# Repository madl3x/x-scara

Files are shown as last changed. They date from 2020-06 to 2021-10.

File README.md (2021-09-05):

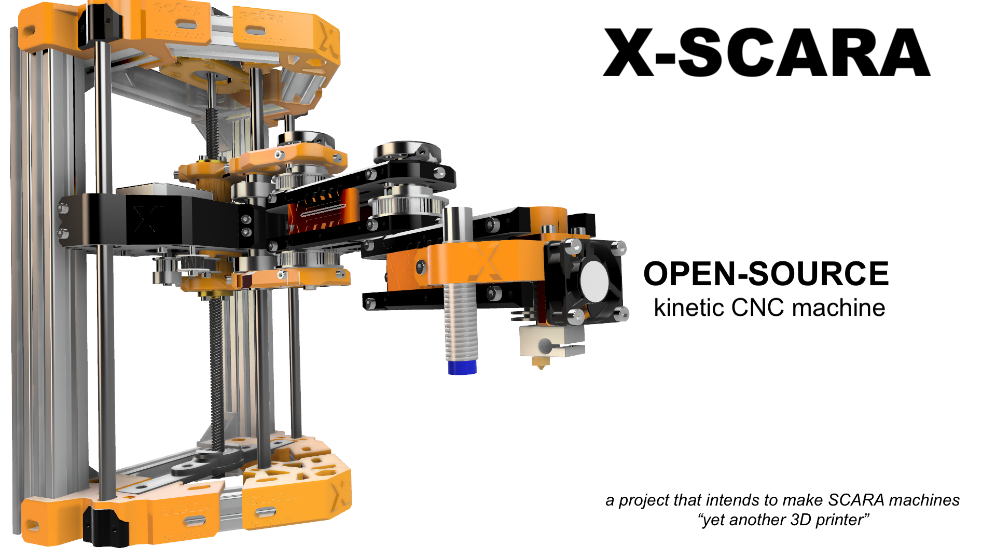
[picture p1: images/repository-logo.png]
X-SCARA


Objective
===
**X-SCARA** is a project that intends to bring the SCARA mechanical model to the world of open-source 3D printing machines, with the same functionality and ease of use as the other popular mechanical models (e.g.: Cartesian, CoreXY, Delta).

    Building, configuring and calibrating the X-SCARA machine must be painless.
    That is our goal!

Hardware
===

    Updates: 
    - X-SCARA hardware is now at revision 5!
    - Added test-part accessory to calibrate your printer before you start printing X-SCARA
    - Added heated bed support directly connected to the X-SCARA frame

The hardware section will contain everything you need to build **X-SCARA**, from the *B.O.M.* to STL files and detailed assembly instructions. 

Check the [hardware section here](hardware/README.md) and if you want to check for updates and/or new accessories take a look at the [changelog](hardware/CHANGELOG.md).

Firmware
===
    Updates:
    - X-SCARA firmware version is now 0.4 BETA!
    - All basic functionality (homing, bed-leveling, tuning segmented movements) implemented & working
    - Added coordinate transformation modes to support bed-leveling (`M360 M2` - probe mode)
    - Implemented homing sequence `G28` 
    - Modified UBL (Unified Bed Leveling) to support **X-SCARA**'s kinematic model
    - Integrated bed-leveling support `G29`
    - Applying bed leveling for planar moves when bed-leveling is activated
    - Modified `M665` for configuring machine's settings
    - EEPROM support to save most important configuration options

For firmware build and configuration follow [these instructions](firmware/README.md).

 if you are already using it check the [changelog](firmware/CHANGELOG.md) for any updates.

Calibration procedure
===
Read [here](CALIBRATION.md) more about you can calibrate **X-SCARA** and start printing.

Credits
===
Author and maintainer of this project is *Alex Mircescu*.

X-SCARA parts and assembly were fully designed in *Autodesk Fusion 360*.

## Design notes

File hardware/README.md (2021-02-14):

Sets
===

Hardware for X-SCARA is organized in sets. Current sets are `frame`, `arm` and `accessories`. 

For printing and assembly instructions of:

 * frame -> [go here](frame/README.md)
 * arm -> [go here](arm/README.md)
 * accessories -> [go here](accessories/README.md)

BOM
===
Bill of materials is available per set. Each set will publish the list of parts required to build it.

Changelog
===
See the full changelog [here](CHANGELOG.md).

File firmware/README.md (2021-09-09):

About
===

Firmware is based on *Marlin 2.x* with modifications that applies specifically to the **X-SCARA** machine. 

The firmware is in BETA stage for the moment with support for homing, bed leveling and machine calibration.

Build instructions
===
Use [this guide](CONFIGURE.md) to configure your firmware before build.

Changelog
===
With each version **X-SCARA** gets improved, check the [changelog](CHANGELOG.md). 

Gcodes
===
Use [this page](GCODES.md) to understand **X-SCARA** specific commands.

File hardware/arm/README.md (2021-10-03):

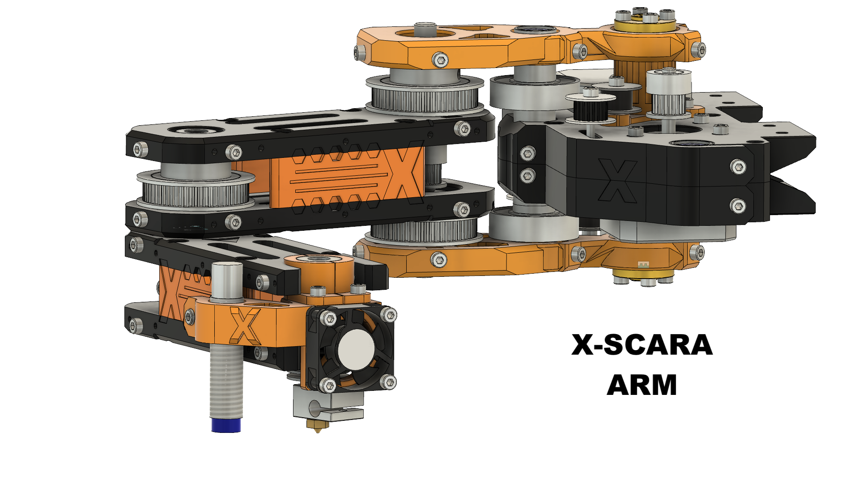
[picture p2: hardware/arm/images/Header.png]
header


Bill of materials
===

Rods
* 1 x 8 mm rod 80 mm length (or hollow axis)
* 1 x 8 mm rod 40 mm length (or hollow axis)
* 1 x 8 mm rod 60 mm length (or hollow axis)

Linear and radial bearings
* 4 x LM8UU linear bearings 
* 1 x LM8LUU linear bearing
* 6 x 623 radial bearings (OD/ID/T 10x3x4)
* 2 x 6002 radial bearings (OD/ID/T 32x15x9)
* 5 x 608 radial bearings (OD/ID/T 22x8x7)

Pulley and belts
* 3 x 280 mm 2GT closed belt
* 2 x 20 teeth 2GT inner bore 5 mm pulley (motor shaft) 
* 1 x 20 teeth 2GT inner bore 8 mm pulley
* 2 x 20 teeth 2GT inner bore 3 mm idler
* 2 x 20 teeth 2GT inner bore 3 mm idler without teeth
* 3 x 60 teeth 2GT inner bore 8 mm

Screws and nuts
* 2 x Tr8 Z-Nut (1 is mandatory, 2 are optional) 
* 70 x M3x10 mm socket head screw
* 20 x M3x12 nnm socket head screw
* 20 x M3x15 or M3x16 mm socket head screw
* 10 x M3x20 mm socket head screw
* 10 x M3x30 mm socket head screw
* 100 x M3 nuts (2mm thick)

Motors
* 2 x NEMA 17 motor 

Endstops
* 2 x Neodium 5x5 mm cylindrical magnets (for endstops)
* 2 x Hall-effect endstops

CAD
===
For a complete preview of the the assemblies, visit these links:
* [Complete arm assembly](https://a360.co/2YkuguU)
* [Base arm assembly](https://a360.co/3c0eRo9)
* [Shoulder assembly](https://a360.co/3dAIDj8)
* [Elbow assembly](https://a360.co/2B50gKS)

Printed parts
===

| Part | Count | Picture |
| --- | ----- | :---: |
| **BASE** | | |
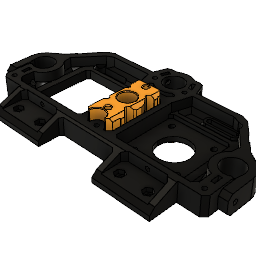
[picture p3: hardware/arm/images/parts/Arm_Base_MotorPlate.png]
sides
| Arm_Base_MotorPlate <td> 2<td rowspan=2>  |
| Arm_Base_ZPlate_Mid_NutHolder| 1 | |
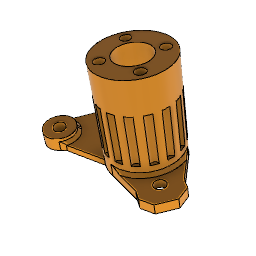
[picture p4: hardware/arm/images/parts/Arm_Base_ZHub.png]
ZHub
| Arm_Base_ZHub_Top <td> 1  <td rowspan=2>  |
| Arm_Base_ZHub_Bottom | 1 | |
| **SHOULDER** | | |
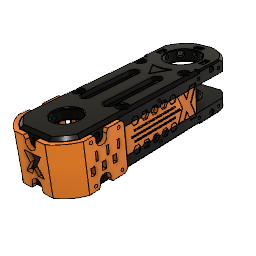
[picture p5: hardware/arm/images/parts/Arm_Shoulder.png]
| Arm_Shoulder_Plate_Top <td> 1<td rowspan=5>  |
| Arm_Shoulder_Plate_Bottom | 1 | |
| Arm_SideWall_Left | 1 | |
| Arm_SideWall_Right | 1 | |
| Arm_Plates_Cover | 2 | |
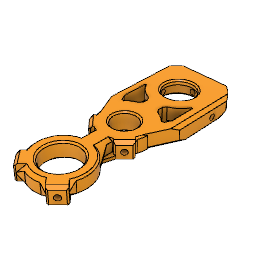
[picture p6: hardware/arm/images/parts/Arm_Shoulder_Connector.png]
connector
| Arm_Shoulder_Connector | 2 |  |
| **ELBOW** | | |
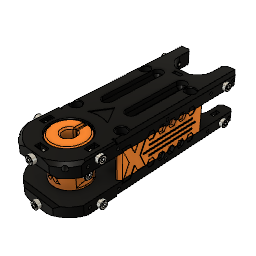
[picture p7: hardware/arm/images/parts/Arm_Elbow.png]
| Arm_Elbow_Plate_Top <td> 1<td rowspan=5>  |
| Arm_Elbow_Plate_Bottom | 1 | |
| Arm_Elbow_RodHub | 1 | |
| Arm_SideWall_Left | 1 | |
| Arm_SideWall_Right | 1 | |
| **E3D MOUNT** | | |
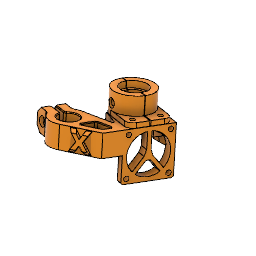
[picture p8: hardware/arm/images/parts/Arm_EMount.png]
| Arm_EMount_Base_ABL <td> 1<td rowspan=3>  |
| Arm_EMount_Base_Left | 1 | |
| Arm_EMount_Base_Right | 1 | |
| **ENDSTOPS** | | |
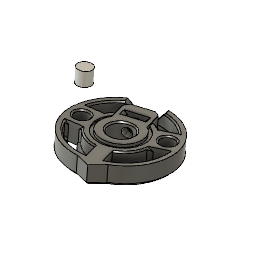
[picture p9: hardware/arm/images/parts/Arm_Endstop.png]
endstop
| Arm_Endstop | 2 |  |

Assembly
===
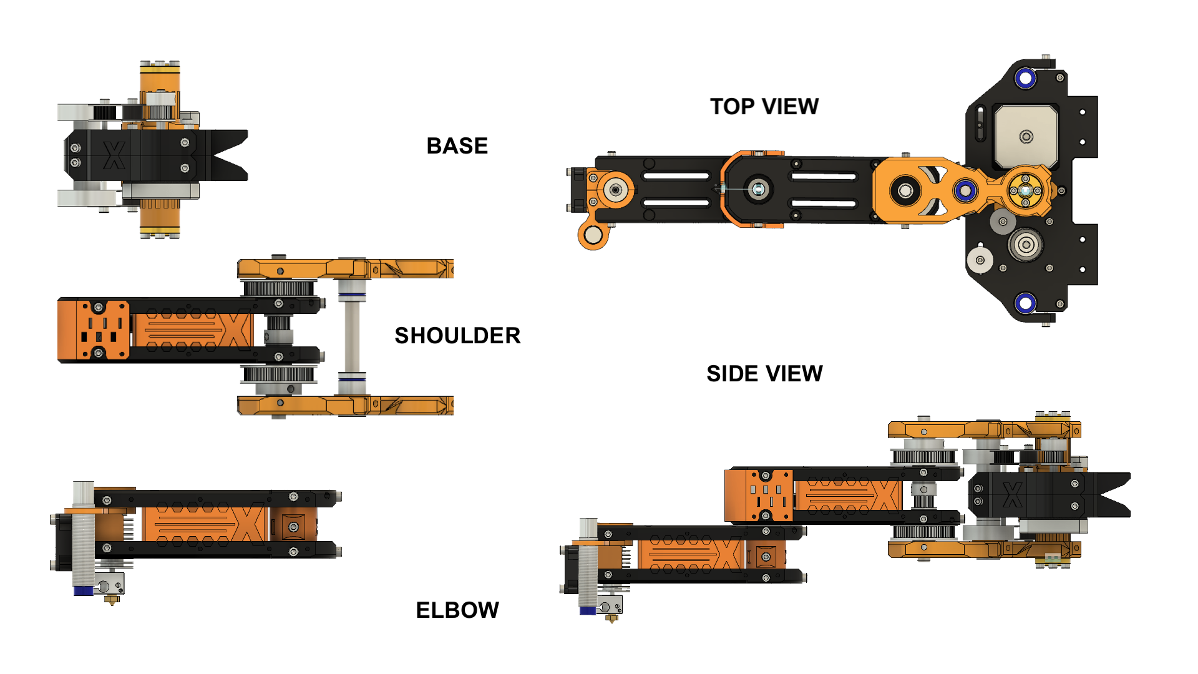
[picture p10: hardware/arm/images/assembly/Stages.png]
 

The arm assembly can be split into five separate stages: 

1. Base assembly
2. Shoulder assembly
3. Elbow and extruder mount assembly
4. Connecting shoulder and base
5. Connecting the arm to X-SCARA frame 
6. Mount the endstops

These parts will then connect together and form the entire arm. The arm can later on be coupled to the X-SCARA frame.
You can fully assemble the arm and test it, separately from the frame.

Stage 1 - Arm Base
===
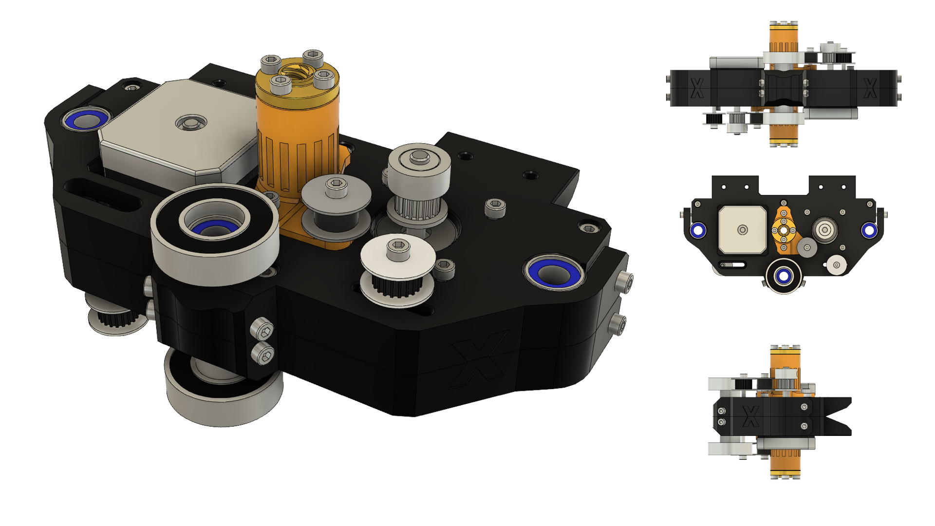
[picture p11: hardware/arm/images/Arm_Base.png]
 

## For a full preview of this assembly go [here](https://a360.co/3c0eRo9).

Step 1 - Join the two Z-Plates
---
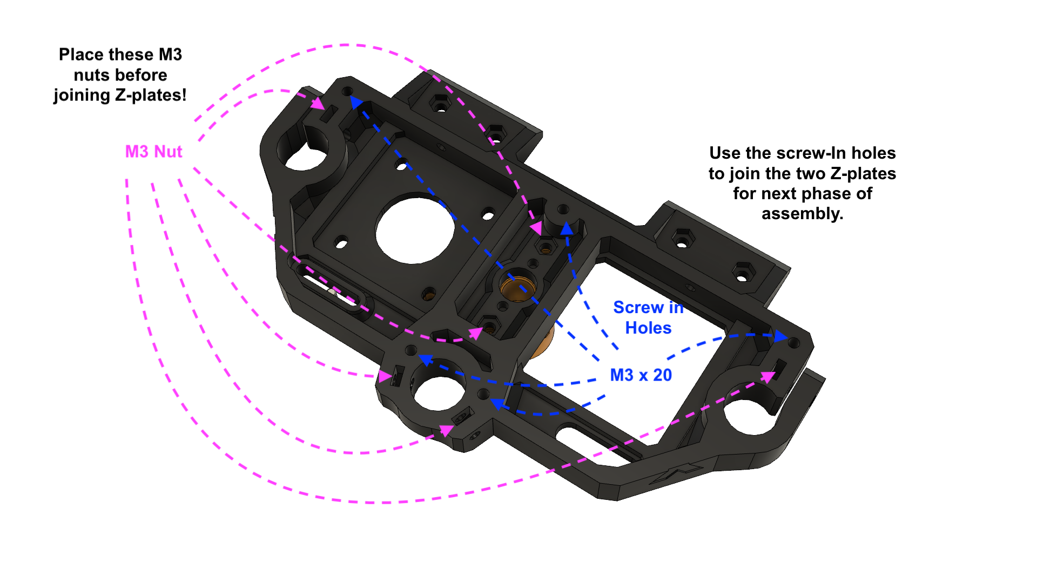
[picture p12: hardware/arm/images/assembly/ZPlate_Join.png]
join z-plates


The *Arm_Base_MotorPlate* must be printed twice. They are designed to be complentary, so one can be placed on top of the other.
Before doing so, place the following M3 nuts first and also place *Arm_Base_ZPlate_Mid_NutHolder* inside the Z-Plate to heep the nuts from falling.

Step 2 - Attach linear bearings, NEMA motors and Z-hub
---
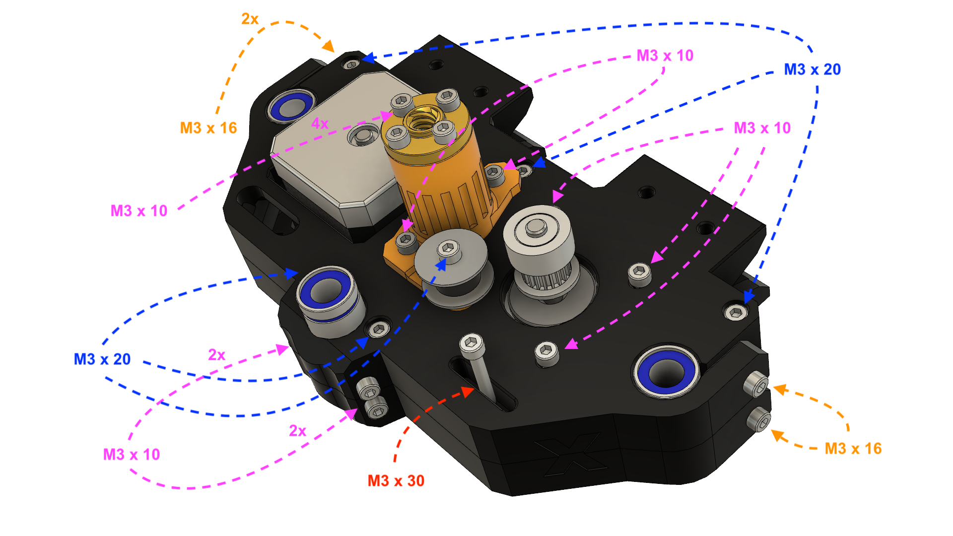
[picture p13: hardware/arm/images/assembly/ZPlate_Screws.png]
z-plate assembly


Above is the screw map of the assembly, it will guide you throughout this step.
Attach the parts to the z-plates, in this prefered order:

1. Tighten the **M3x20** screws for the screw-in holes mentioned in **Step 1**

This will join the two Z-plates together. 
If the screws tend to fall out from the screw-in holes, use some Thread Lock Glue to hold them in place. 
The part's structural resistance doesn't rely on those, don't worry. 

2. Attach the **NEMA17** motors with three **M3x10** screws, leaving the fourth one free
3. Attach the Z-hubs with two screws for each
4. Place *only one* trapezoidal Z-nut on one Z-hub and screw it down

The second Z-nut is optional, you can use it to eliminate backlash, but it must be tighten after the base is mounted on the lead screws.
Otherwise, if the Z-Nuts are not properly aligned with the lead screw pitch, it may lock itself on the Z screw.

5. insert the **LM8UU** and **LM8LUU** bearings and secure them with the corresponding screws

After this, the part should feel like one solid piece. The metal linear bearings should properly join both Z-plates.

6. Attach the center idler pulley and secure it down with a **M3x20** screw (place washers!)

Place one or more washers between the idlers and the Z-hub. 

7. Attach the drive pulley to the motor shaft 

Step 3 - Install adjustable pulley
---
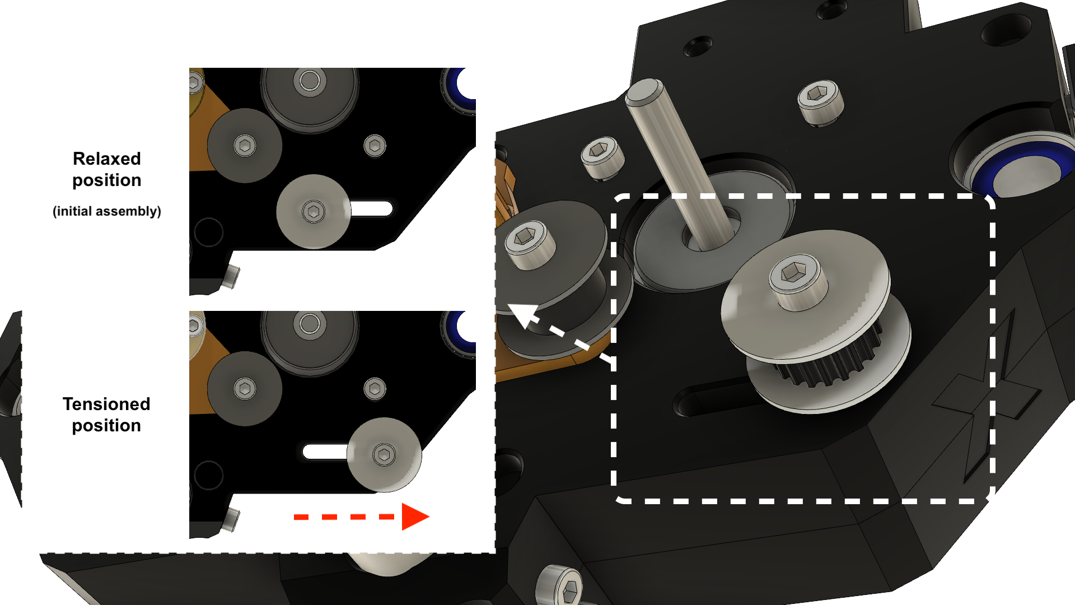
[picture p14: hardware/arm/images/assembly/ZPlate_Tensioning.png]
belt tensioning


1. Place the pulley on **M3x30** screw and add washers to align it with the motor pulley
2. Place the screw in *relaxed* position
3. insert an M3 nut using the opening on the other side of the Z-plate and tighten it gently 

This may seem a bit difficult at first. Use a pair of tweezers to help you out with placing the M3 nut.

The installation of the pulley will be finalized when the belt is installed.

Step 4 - Attach the 6002 bearing and align belt components
---

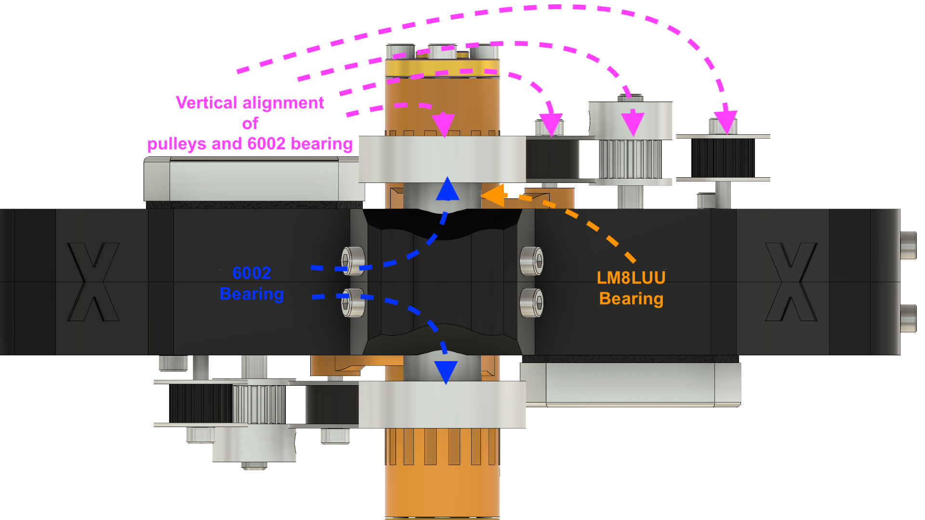
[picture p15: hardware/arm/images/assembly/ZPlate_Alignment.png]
belt path alighment

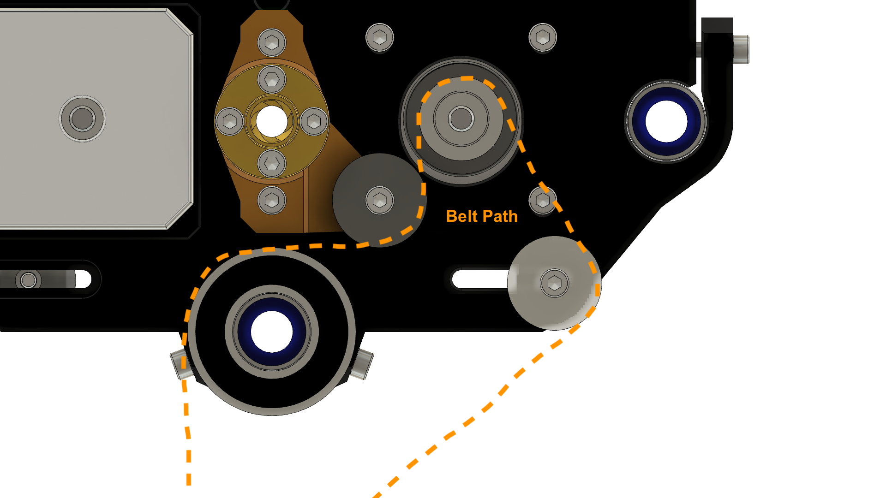
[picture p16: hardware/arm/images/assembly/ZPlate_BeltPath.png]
belt path


Stage 2 - Shoulder component
===
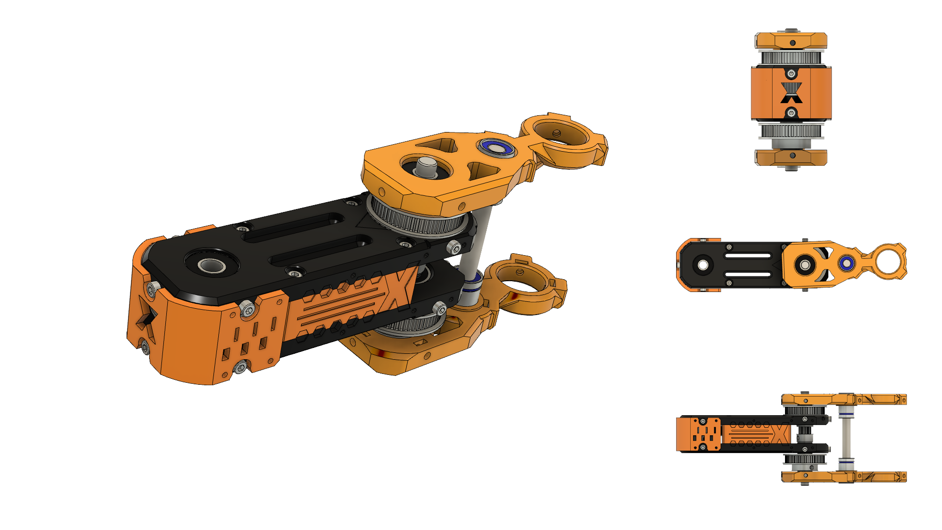
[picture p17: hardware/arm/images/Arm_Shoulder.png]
shoulder


## For a full preview of this assembly go [here](https://a360.co/3dAIDj8).

Step 1 - Install 3 x 608 bearings and the drive pulley
---
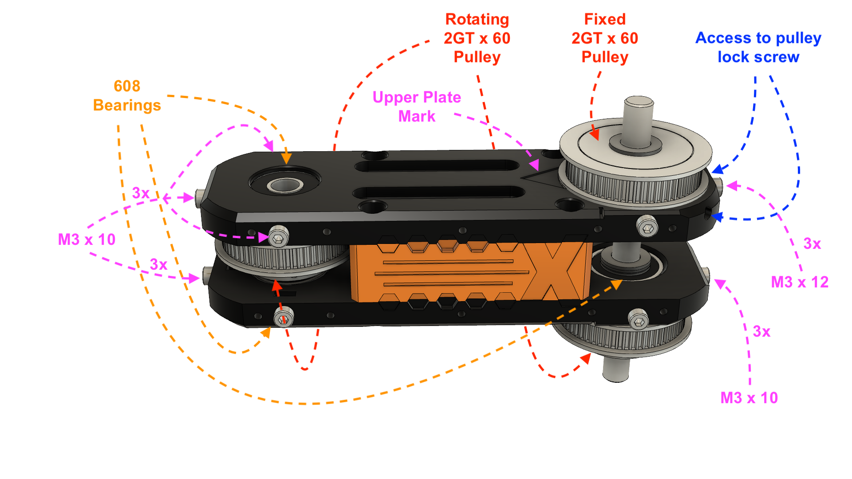
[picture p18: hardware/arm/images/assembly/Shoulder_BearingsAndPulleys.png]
bearing and drive pulley


Each 608 bearing is connected to the arm plate using three **M3x10** screws. 
Tighthen the screws for each bearing in the same order, to avoid missalignment. 

Step 2 - Install the two 2GT x 60 drive pulleys
---
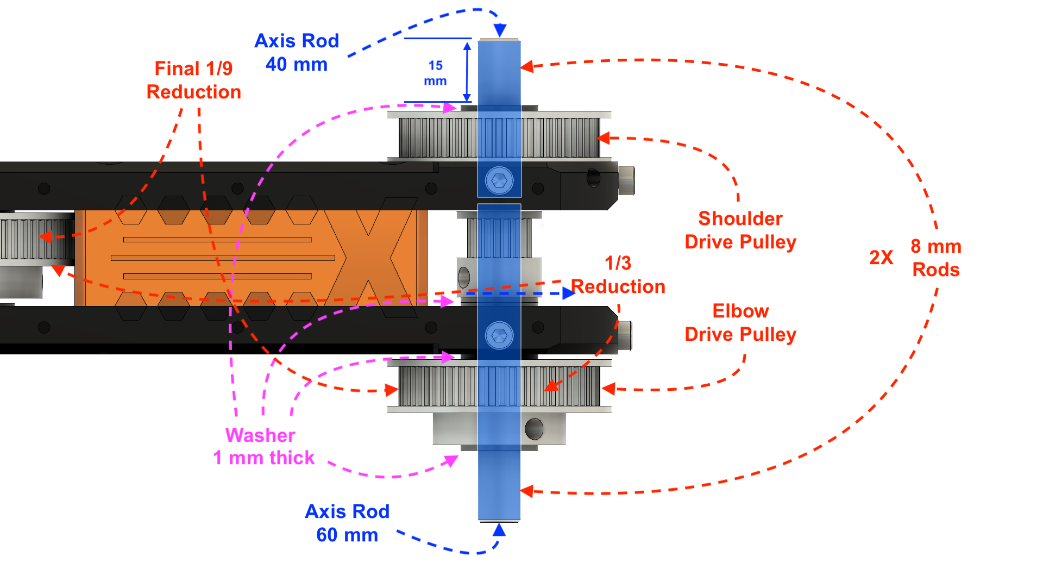
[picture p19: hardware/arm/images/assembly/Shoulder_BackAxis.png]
shoulder back axis


Connect the top **2GT x 60** **shoudler drive pulley** first, with the 8mm rod inserted and attach it to top arm's plate in the same way you connected the 608 bearings. If you need to adjust the rod's height afterwards, you can use the two openings on the back of top plate to access the dowel pins of the pulley and losen the screws. 

Make sure you align the pulley first to get to be able to reach those:
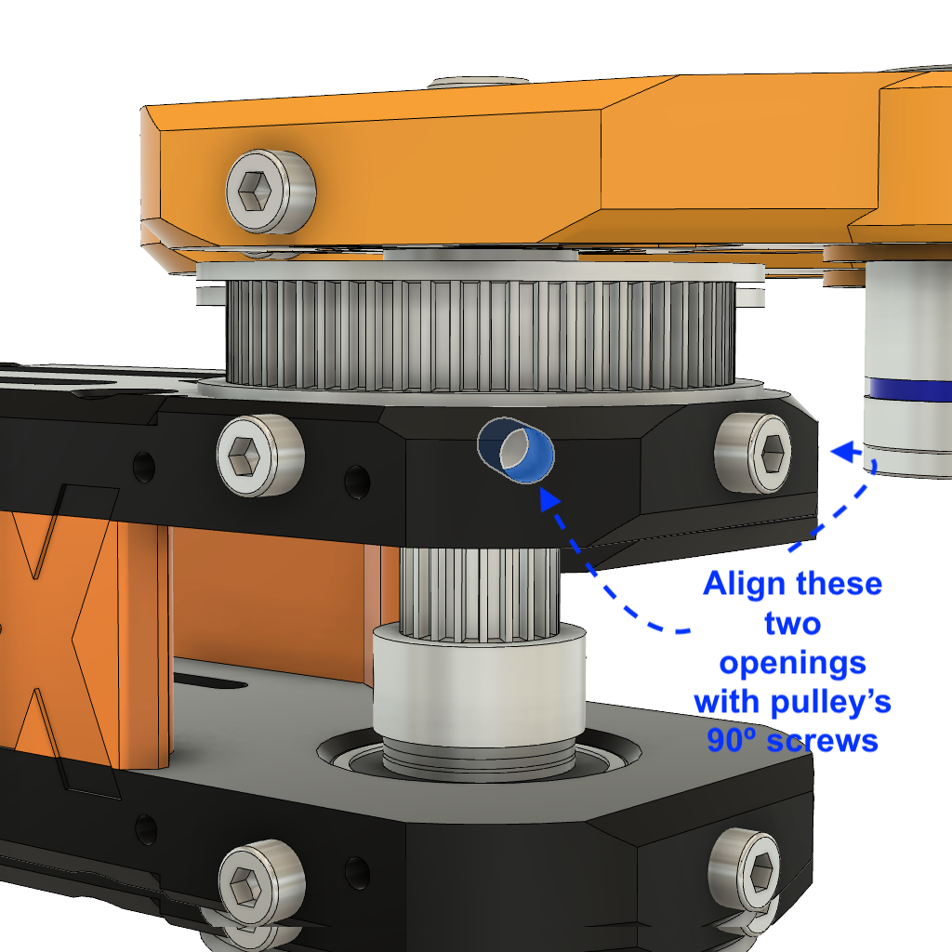
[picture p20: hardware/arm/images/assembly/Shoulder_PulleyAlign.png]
shoulder pulley alignment


For the bottom **2GT x 60** **elbow drive pulley**, first insert the 60 mm rod and tighten it. Pass the rod through the 608 bearing on the bottom plate, with a washer between the bearing and pulley. Add two (or more) washers on top of the axis and them insert the **2GT x 20** pulley. 

Press the **2GT x 20** pulley agains the **2GT x 60** pulley to create a firm grip of the bottom plate, then secure it by screwing the dowel pins on the **2GT x 20** pulley.

Step 3 - Install tensioning bearings
---
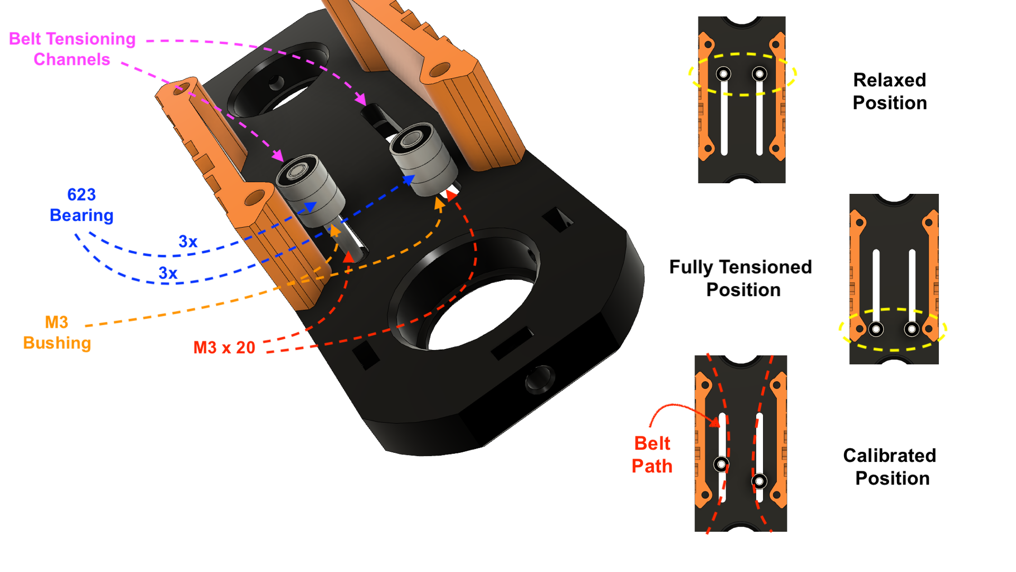
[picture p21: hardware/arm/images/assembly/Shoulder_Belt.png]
shoulder


Use 2 sets of 3 x **623 bearings** each and one *M3x20* screw as axis, to install them as tensioning idlers. 
Place the screw with the head facing down (towards the bottom plate) and the M3 nut on top of the last bearing.

Place the two tensioning idlers in the relaxed position, as seen above.

Step 4 - Elbow axis
---
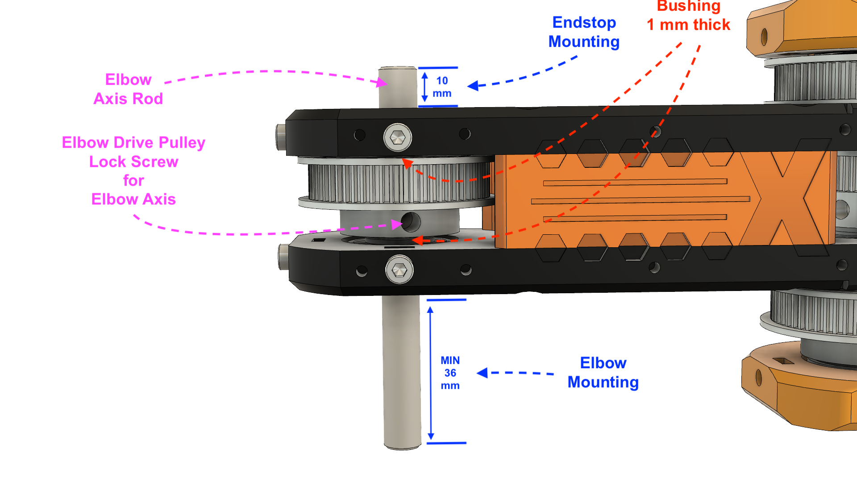
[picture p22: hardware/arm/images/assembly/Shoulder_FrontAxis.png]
shoulder


Insert the elbow rod to the **2GTx60** pulley and connect it to the bottom plate, by inserting it to the front **608** bearing.

Step 5 - Place the belt
---

Place the belt between the back **2GT x 20** pulley and the front **2GT x 60** **elbow drive pulley**. Make sure the pulleys are aligned. If not, add or remove washers to raise or lower the **2GT x 20** on the back.

Adjust the tensioning idlers, just to hold the belt in place. Don't fully tension the belt yet.

Step 6 - Connect the two shoulder plates
---
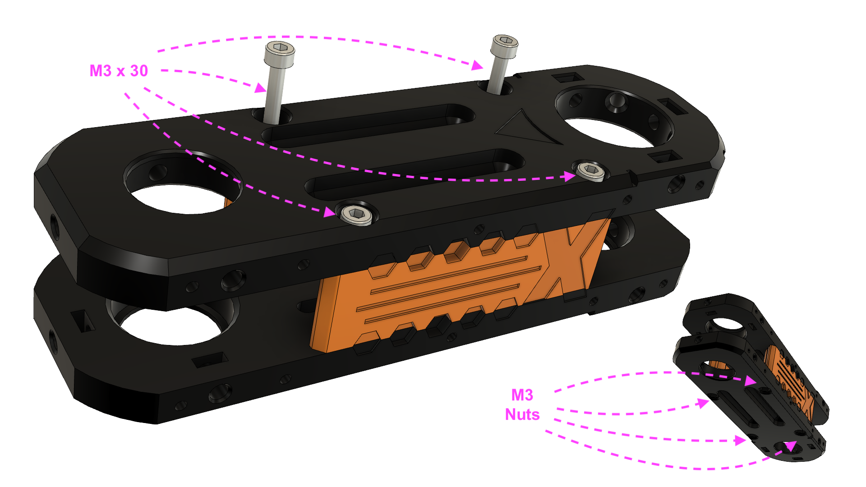
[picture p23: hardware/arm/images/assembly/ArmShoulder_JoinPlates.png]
shoulder plates


Connect the bottom plate and the top plate via the four **M3x30** that will pass through **Arm_SideWall_Left** and **Arm_SideWall_Right**. 

Install only two out of the four **M3x30** screws so the side walls can pivot and give you access to tensioning idlers.

Step 7 - Tension the belt
---
Tension the idlers and secure the screws so the idlers are firmly set in position.

The front axis should not present any noticeable backlash after tighning, but in the same time, the elbow drive pulley should be moveable by hand with ease. 

Step 8 - Prepare the shoulder connector
---
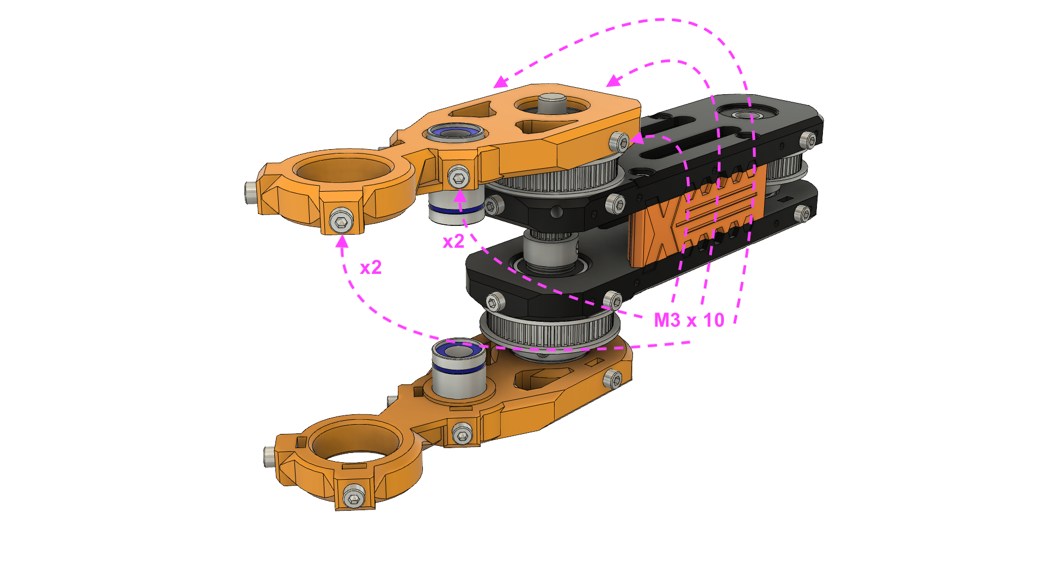
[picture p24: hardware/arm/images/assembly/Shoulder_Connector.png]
shoulder connector


The **Arm_Shoulder_Connector** wil connect the plates to the Arm base. Prepare it by mounting the two **608** radial bearings the same way you did with the shoulder plates. 

Attach the two **LM8UU** linear bearings to the connector and secure them with 2 x **M3x10** screws for each. 

Also, attach the **M3x10** screws on the back-side of the connector, but don't tighten yet. 
These will be used to attach the shoudler to the hub component of the base.

Step 9 - Close arm's side walls
---
Add the two remaining **M3x30** screws to finalize the shoulder assembly. 
Tighten all four side wall screws.

Step 10 - Install cover  (optional)
---
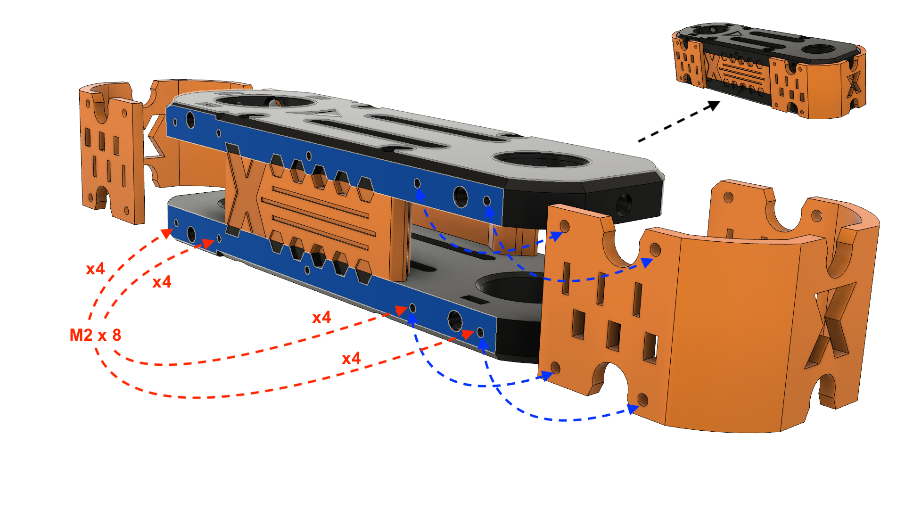
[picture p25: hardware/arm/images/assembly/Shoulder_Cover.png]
shoulder connector


Cover can be installed on the front of the shoulder arm, and as well on the back.

Stage 3 - Elbow
===
elbow

## For a full preview of this assembly go [here](https://a360.co/2B50gKS).

The hard part is gone. Now we need to assemble the elbow and the extruder mount. This is how it must look when finished.

Step 1 - Connect elbow plates
---

Connect bottom and top elbow plates using four **M3x30** screws, just like on the shoulder plates. Pass the screws through **Arm_SideWall_Left** and **Arm_SideWall_Right** parts.

Step 2 - Connect elbow's hub to shoulder's front axis
---
elbow hub

Place a washer between the hub and the **608** bearing in the bottom shoulder plate. Connect the hub to the 8mm rod and tighten the side **M3x10** screws.

Step 3 - Connect the assembled plates to rod hub
---
Insert and tighten the six **M3x10** screws to firmly connect the elbow plates to the shoulder.

Step 4 - Assemble the extruder mount
---
elbow hub

It can be assembled separately. Get your *E3D* hotend and plece it between the two **Arm_EMount_Base** parts. Connect the parts together by mounting the **Arm_EMount_Base_ABL** part. Screw directly in plastic, no metal nuts are required.

Step 5 - Install the extruder mount
---

Two **M3x15** can be used to connect the extruder mount to the top elbow plate. 

To ensure the hotend doens't pivot around these two while printing, two additional **M3x25** screws can be mounted on the bottom, to get a firm grip directly on the **E3D**'s radiator.

Stage 4 - Attach shoulder to arm base hub
===
base connect

Take the previosly assembled **Arm_Shoulder_Connector** part and connect the base of the arm with the
shoulder assembly. Connect the base hub with the shoulder connector and the later one with the shoulder back axis.

Tighten the four screws on the back of the **Arm_Shoulder_Connector** as indicated. Now the entire arm should be one working piece. 

Stage 5 - Atach the entire arm to the frame
===

final

* Remove all rods and the the lead screw from your frame. Place the frame on the back side for ease of manoeuvre.
* Install the side 8mm rods partially and insert the rods through the arm assembly. 
* Insert the two rods all the way and secure them with the clamps
* Insert the third rod and secure it

Test if the arm glides smoothly and if not, make adjustments on the frame for proper alignment of the rods.

* Insert the lead screw from the bottom side of the frame
* Screw it through the arm's Z-nut

If you are using two Z-nuts make sure the arm can climb and descend easily. 
Adjust the screws on one of the Z-nuts to make sure it does not add too much tension on the lead screw.

* Connect the lead screw to the Z motor with the coupling shaft

Stage 6 - Mount the endstops
===
endstops

X-SCARA uses magnetic endstops for homing. The endstops are mounted on the shoulder and elbow axis directly and they are secured using an **M3** screw.

For more details check the firmware calibration guide.

Done
===
Nicely done. Now assemble the [frame](../frame/README.md) if you haven't done so by now.

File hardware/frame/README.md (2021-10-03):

header

Bill of materials
===

Each element marked with (Z) can be extended by a given offset if you intend to make the SCARA higher than originally designed.

Aluminum extrusions
* 2 x 20x40 300mm aluminum profile (Z)
* 2 x 20x20 130mm aluminum profile
* 8 x 20x20 60mm aluminum profile 

Brackets
* 8 x 20x20 Corner Cast bracket 

Rods and lead screw
* 3 x 8mm 300mm rods (Z)
* 1 x Tr8/x 250 mm lead screw (Z) (2 mm pitch preferred)

Screws and nuts

* 50 x Button Head M5 x 10mm Screws
* 50 x M5 Drop In Hammer T-Nuts for 2020 (OR 50 x M5 square Nuts for 2020)
* 15 x socket Head Screw M3x10
* 10 x socket Head Screw M3x12
* 20 x M3 nuts (2 mm thick)
* 2 x T-Nuts (corresponding to your chosen lead screw) 

Others
* 1 x 608 bearing (OD/ID/T 22x8x7)
* 1 x NEMA 17 motor 
* 1 x Flexible Shaft Coupling 8x5 mm

CAD
===
For a complete preview of the frame model check this Autodesk Fusion 360 [shared link](https://a360.co/2UZK4Bm).

Printed parts
===

| Part | Count | Picture |
| --- | ----- | :---: |
| Frame_Plate_TipConnector | 2 | tip |
| Frame_Plate_Side_Left <td> 2  <td rowspan=3> sides |
| Frame_Plate_Side_Right | 2 |
| Frame_Plate_Side_RodClamp | 4 |
| Frame_Z_BearingPlate <td> 1  <td rowspan=2> bearing |
| Frame_Z_BearingHolder | 1 |
| Frame_Z_MotorPlate <td> 1  <td rowspan=2> motor |
| Frame_Z_MotorConnector | 1 |

Assembly
===

Step 1 - Assemble the bottom plate
---

bottom plate down
bottom plate up

Make sure when you connect these parts that the aluminum profiles have a corect 90º angle, before tightening the screws.

Don't tighten the screws too hard to allow adjustments at the end of the assembly. 
This is especially valid for the Z bearing plate, which requires adjustment of the Z lead screw after the arm
is installed.

Step 2 - Assemble top plate
---

top plate down
top plate up

The top plate is very much similar with the bottom plate, with the exception of the Z-Motor mount. 

Don't tighten the screws too hard for the motor mount. 
Like the bearing plate, it will require adjustments after arm installation.

Step 3 - Assemble the plates on the back frame
---

top plate down

This is somewhat straight-forward. Make sure the plates are parallel after assembly.

Step 4 - Assemble the rods and lead screw (temporarly)
---

top plate down

This parts will get their final assembly after the arm is fully assembled and installed. 
Place them just to check for missalignments.

Done
===
Nicely done. Now assemble the [arm](../arm/README.md) if you haven't done so by now.

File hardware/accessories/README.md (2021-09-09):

Test-part
===
Get it from [here](test-part/README.md).

Designed to test your 3D printer profile, to make sure the X-SCARA parts you are printing fit well with the metal hardware.

Bed mount
===
Get it from [here](fixed-bed-mount/README.md).

This is a fixed bed mount for `100` mm x `100` mm heated bed.

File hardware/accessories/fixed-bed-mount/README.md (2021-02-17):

fixed-bed-mount

About
===

Every 3D printer has a heated bed, so why shouldn't **X-SCARA** have one too?

This accessory is designed mainly for the *OpenBuilds mini heated bed* heaters (see picture) and it works by connecting the build plate firmly to the **X-SCARA** frame. This rigid connection enables you to do precise bed leveling calibration and to keep it consistent across multiple prints. Needless to say this will avoid ruining your print if you accidentally hit X-SCARA while working.

The *OpenBuilds mini heated bed* can easily reach 100ºC, allowing you to build with materials like *PET, PET-G, TPU*.

Bill of materials
===

Screws and nuts
* 6 x M3x12 screws (or M3x20)
* 4 x M3x20 screws (or M3x30)
* 4 x M3x25 screws (or M3x30)
* 14 x M3 nuts (2.2mm thick)

Electronics
* 1 x NTC 100k B3950 glass or metal thermistor 
* 1 x 100mm x 100mm heated bed (recommended OpenBuilds mini heated bed - check [ooznest.co.uk](https://ooznest.co.uk/product/openbuilds-mini-heated-bed/))

Others
* 4 x bed compression springs (OD 8mm, 20-25mm height)
* aluminum/glass build plate 100 mm x 100 mm

Printed parts
===

| Part | Count | Picture |
| --- | ----- | :---: |
| Acc_FixedBedMount_Arm | 1 | sides |
| Acc_FixedBedMount_HeaterSupport | 1 | sides |
| Frame_Plate_TipConnector_FixedBedMount</br> (replaces `Frame_Plate_TipConnector`) | 1 | ZHub |

    Make sure you print the test part to check how your prints fit metal hardware.

Please note that the `Frame_Plate_TipConnector_FixedBedMount` replaces the `Frame_Plate_TipConnector` part from the frame set, to allow `Acc_FixedBedMount_Arm` part to connect to it via 4x **M3x12** screws.

Assembly
===

Step 1 - Assemble the accessory
---
instructions

The assembly is pretty much straight forward:

* place all M3 nuts at their designated places in `Acc_FixedBedMount_HeaterSupport` before starting assembly
* connect the heater, the aluminum/glass build plate and the springs to the `Acc_FixedBedMount_HeaterSupport` part and screw in firmly
* connect the `Acc_FixedBedMount_Arm` to the support you just assembled (follow the same instructions you used for building your frame [here](../../frame/README.md))
* connect the modified `Frame_Plate_TipConnector_FixedBedMount` to your frame (replace the old `Frame_Plate_TipConnector` if necessary)
* connect the arm to the new frame part

Step 2 - Firmware configuration
---
Just make sure your scara offset is set to `110` mm in `Configuration.h`:

```C
 #define SCARA_OFFSET_Y    -110    // (mm)
```
For more details check the [configuration guidelines](../../../firmware/CONFIGURE.md).

Alternative mountings
===

In this set you also have a part called `Acc_FixedBedMount_AlternativeArm`. 

This part is an alternative for connecting the `Acc_FixedBedMount_HeaterSupport` to the frame without requiring the replacement of any frame parts. It connects directly to the `Frame_Plate_TipConnector` part and stays secured via two screws that push on the plastic part when fastened.

The downside of this part is that is not as solid as this design and the bed can move up and down if hit.
Check this [video](https://www.instagram.com/p/CK_2IUaI0A7/) to see it in action.

Another alternative will be to screw `Acc_FixedBedMount_HeaterSupport` directly on a fixed surface, using M3 screws. The part provides multiple 3mm drills to allow you to fix it in place on wood or other surfaces.

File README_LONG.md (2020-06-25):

X-SCARA

Types of SCARA
===
SCARA mechanical model divides in two slightly different concepts: *serial SCARA* and *parallel SCARA. 

*Parallel SCARA* is a mechanical concept that uses four joints and four segments, two of which are mirrored to compensate for intertia in fast movements.

*Serial SCARA* only uses two segments and two corresponding joints to accomplish the same action. Both parallel and serial SCARA designs uses two rotary actuators (e.g. two motors) to move in the Cartesian space.

History
===
One of the first successful open-source parallel SCARA designs was the [Morgan Scara](https://en.wikipedia.org/wiki/RepRap_Morgan), built by an african engineer in 2013 with the objective to create really affordable printers. 

Since then, only a handfull of counter designs were published in the open-source community, most of them inheriting same design priciples from Morgan's.

For the serial SCARA, most notable is the [MP-Scara](https://www.thingiverse.com/thing:2487048), *MP* standing for *M*ostly *P*rinted.

Motivation
===
For a hardware perspective SCARA is an easy to build 3D printer, but hard to configure and find software support for. The documentation is scarse and the calibration process counter-intuitive even for 3D printing experts.

Delta printers share the same type of mechanical complexity with SCARAs, but they managed to get a respectable place among 3D printers, while the SCARA model is lacking behing circling around the same design principles that made it known.

For this, and not only, this project intends to make a step forward and propose a new mechanical design and prepare a firmware to make it work as simple as a Cartesian.

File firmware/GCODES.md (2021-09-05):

GCodes
===
The following document documents the **Gcodes** implemented or modified by **X-SCARA** implementation

X-SCARA Specific GCodes
===

M360 - X-SCARA - Change Coordinates Transformation
----

```
 Parameters:
 
 M<int>  - transformation mode (0 or 1)
 
            0 - cartesian (default) 
                current X and Y coords. are cartesian coords. pointing to extruder's nozzle
 
            1 - angular (used by G28, when homing) 
                current X and Y coords. are angular coords. of shoulder and elbow position)

            1 - probe (used by G29, when leveling bed) 
                current X and Y are cartesian cords pointing to probe's center
```

This command will instruct the **X-SCARA** machine to switch the entire coordinate mapping system to cartesian, angular or probe mode.

> Use this explicitly only for testing and calibration!

#### `Cartesian mode`

In cartesian mode **X-SCARA** will automatically transform the `X` and `Y` coordinates to angular positions for the shoulder and elbow joints, using inverse kinematics. This is the normal mode, using during printing.

#### `Angular mode`

The `M360 M1` command allows you to move either the shoulder, or the elbow to an angle you expect and observe the result, usign standard GCode commands (e.g. `G0`, `G1` or `G92`). For example, after invoking `M360 M1` you can move the arm's shoulder to 0º using `G0 X0` or the elbow to 90º using `G0 Y90`. 

Used internally when homing with `G28`.

#### `Probe mode`

The `M360 M2` command will switch to a transformation mode, similar to `M360 M0`, but this time pointing to the probe's center, instead of the extruder's nozzle. Used internally by bed-leveling `G29` commands. 

Used internally when running bed-leveling commands with `G29`.

M361 - X-SCARA - Move joints to angular position
----

```
 Parameters:
 
 S<float>  - Move to given shoulder angle (in degrees)
 E<float>  - Move to given elbow angle (in degrees)
 I<booL>   - Add the given to the current position instead of setting them
```

This command is useful to move the machine's joints to a specific angular position. 
When invoked, it will report back the angular position of each joint and the coresponding cartesian coordinates, even if run without arguments.

M362 - X-SCARA - Set current joints position
----
```
 Parameters:
 
 S<float>  - Set the shoulder angle to this value (in degrees)
 E<float>  - Set the elbow angle to this value (in degrees)
```

This command is the complement of `G92` command for angular positioning. `G92` sets the current absolute position for X,Y,Z axis and even E(xtruder), to a given value while `M362` sets the current position of joints, to a given value.

For example, to reset the machine back to its correct position, you could move the arm perfectly straight and then run:

```
M362 E0 S0
```
This command tells the machine the current position is 0º angle for both shoulder and elbow joints. After that, you can move the machine safely in cartesian space.

Please note that the same effect can be obtained using `G92`, after changing the coordinate system to angular positioning using `M360 M1`. 

> Soon to become deprecated! Same as `G92` when using `M360 M1`.

M364 - X-SCARA - Get X-SCARA version
----
```
 Parameters:
 
 D<bool>  - if `X_SCARA_DEBUG` is configured, enable or disabled verbosity
```

Prints the current version of **X-SCARA** implementation.

If `X_SCARA_DEBUG` is enabled in `Configuration.h` enables detailed log tracing using `M364 D1`.

Modified Marlin GCodes
===

G0/G1 - Move to destination
---

**X-SCARA** uses the `G0` command to move directly to destination (without segmented moves) and `G1` command to move to destination using multiple segmented moves.

To configure the number of segments for each move, use `M665 D` command to set the number of segments per second and `M665 M` command to set the minimum segment length. 

> If the `G1` response is choppy and the linear movement is not fluent, lower the number of segments and/or increase the minimum segment length (e.g. `M665 D30 M0.5`).

Check [Marlin documentation](https://marlinfw.org/docs/gcode/G000-G001.html) for more details. 

G28 - Home axis
---

**X-SCARA** will home the `Z` axis using bed-probe and the `X` and `Y` using magnetic endstops. 

The endstops for `X` (shoulder) and `Y` (elbow) axis must be positioned at `-90` degrees.

> When the axis is at `-90` degrees, it point towards machine's `right`. </br>
> When the axis is at `90` degrees, it point  towards machine's  `left`. </br>
> When the axis is at `0` degrees, it point  towards `forward`.

#### XY Homing sequence

The XY homing sequence is designed to avoid crashing the machine as much as possible.

The two axis are marked as `codependent` and can't be homed independently. Running `G28 X` or `G28 Y` or `G28 XY` will have the same effect.

The homing sequence is more elaborate for **X-SCARA** machine, and it happens as follows:

* (1) - Coordinate transformation is set to `angular` (`M360 M1`)
* (2) - X axis (shoulder) moves clockwise until it hits the endstop positioned at `-90º`
* (3) - X axis applies configured home offset (via `M665 X`)
* (4) - X axis moves back to 0º position
* (5) - Y axis (elbow) moves clockwise until it hits the endstop position at `-90º`
* (6) - Y axis applies hconfigured home offset ( via `M665 Y`)
* (7) - Y axis moves back to 0º position
* (8) - Coordinate transformation is set back to `cartesian` (`M360 M0`)
* (9) - Axis are marked as homed
* (8) - Moving to bed center (`X`0 and `Y`0 in cartesian space)

M665 - Set X-SCARA settings
----
```
 Parameters:
 
 D<seg-secs>  - sets the number of segments per seconds for linear moves (default is SCARA_SEGMENTS_PER_SECOND)
 M<seg-min>   - sets the minimum segment length in mm for linear moves (default is SCARA_MIN_SEGMENT_LENGTH)
 S<offset>    - sets the shoulder home offset in degrees (to calibrate homing)
 E<offset>    - sets the elbow home offset in degrees (to calibrate homing)
 X<origin>    - sets the offset on the X axis for bed center position (usually 0, default SCARA_OFFSET_X)
 Y<origin>    - sets the offset on the Y axis for bed center position (default SCARA_OFFSET_Y)
```

This command is used to configure *Delta* printers and also *Scara* machine in *Marlin* Firmware. 
Any of these values can be saved and restored to/from EEPROM using `M50x` G-Code commands.

#### `Tuning segmented moves`
Tune linear movements using `M665 D` and `M665 M` options. If the movement is choppy, lower the number of segments to a more reasonable value (e.g.: `30`) and/or increase the minimum segment (e.g.: to `0.5`).

#### `Aligning bed's center`

If the machine doesn't point at the bed's center correctly, use `M665 X Y` to setup the offset the current known center and save the value in EEPROM using `M500`. For example, running `M665 X-5` will move the bed's center to the right by `5` mm.

#### `Calibrating home position`

This is the one of the most important configurations for **X-SCARA**: **calibrating the home position**.

When setting the endstops for the `X` (shoulder) and `Y` (elbow) axis, most likely you will not be able to mechanically position those at perfectly `-90º` angles. The `M665 X Y` command will allow you to do fine adjustements and save those to EEPROM.

Follow this steps to calibrate the home position:
* (1) - position the `X` and `Y` endstops (the best you can) at `-90º` position
* (2) - home the machine using `G28 XY`
* (3) - move the arm to point forward by running  `M361 S0 E0` (i.e.: set elbow and shoulder angular position to 0º)
* (4) - use the same `M361` command to adjust the angular position for both axis so that the arm gets perfectly straight
* (5) - get the resulted positions and store them as offsets them using `M665 S E`
* (7) - home again using `G28 XY`
* (8) - repeat (2)-(8) until perfect alignment is achieved
* (9) - save the resulted values to EEPROM using `M500`

> Note: bad alignment of shoulder axis will not result in deformed parts, but **improper positioning of the elbow axis will do**.
>

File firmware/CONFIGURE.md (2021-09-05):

Marlin configuration
===
> This is the configuration tutorial for the `0.4 - Beta` firmware!

The two template configuration files you can start from are in `Marlin-2.0.x/config` folder: 
* [Configuration.h](Marlin-2.0.x/config/SCARA/X-SCARA/Configuration.h) 
* [Configuration_Adv.h](Marlin-2.0.x/config/SCARA/X-SCARA/Configuration_Adv.h)

Coordinate mapping
===
To get a glympse of how the cartesian coordinate system is mapped, we have some examples:

* (X0,Y0) - represents the location where the center of the shoulder axis is;
* (X0,Y186) - the location where the center of the extruder nozzle is, when the arm is perfectly straight (shoulder & elbow angle are 0º);
* (X98,Y98) - -"- when shoulder angle is 0º and elbow angle is 90º;
* (x-98,Y98) - -"- when shoudler angle is -90º and elbow angle is 0º;

Configuration.h
===

#### `X_SCARA`
To enable **X-SCARA** support in **Marlin** you need to define `X-SCARA` and `SCARA` compile time options.

#### `X_SCARA_DEBUG`
Activate extensive tracing to the serial console for debugging the implemention(not needed in production).

#### `SCARA_LINKAGE_1`
Length of shoulder to elbow linkage (for **X_SCARA** this is currently `98` mm).

#### `SCARA_LINKAGE_2`
Length of elbow to tip linkage (for **X_SCARA** this is currently `98` mm).

#### `SCARA_OFFSET_X` and `SCARA_OFFSET_Y`
Bed center offset from the real coordinate mapping (if bed is aligned with machine's center, X will be 0).

Default value for **98mm** linkage lengths is `X`:`0` mm and `Y`:`-110`mm.

> Starting with Firmwre **V0.4** `SCARA_OFFSET_X` and `SCARA_OFFSET_Y` are configurable at run-time using `M665 X Y` G-Code and can be saved/restored to/from EEPROM using `M50x` commands.

#### `SCARA_SEGMENTS_PER_SECOND`
The default number of segments per second that **X-SCARA** will use to segment a linear move.

Tune this value according to your Mainboard's processor. For an 8-bit AVR this can range from `30` to `200`, for a 32-bit ARM processor this value can go even higher. If the movement is choppy when you run `G1` gcode, set this configuration to a lower value (e.g.: for 30 segments per second `M665 D30`).

The higher this value is, the more precise the movements will be, with the cost of more CPU usage.

> Starting with Firmware **V0.4** you can configure this setting at run-time using `M665 D` G-Code, and save it to EEPROM using `M500`.

#### `SCARA_MIN_SEGMENT_LENGTH`
The minimum segment width the **X-SCARA** will use for segmented moved. Default is `0.5` mm.

Setting this value higher, will reduce the kinematic overhead and use less CPU for linear movements, but the prints will have more jagged lines. For better precission, reduce this value to the lowest possible and also raise the number of segments using `M665 D` G-Code command.

> Starting with Firmware **V0.4** you can configure this setting at run-time using `M665 M` G-Code, and save it to EEPROM using `M500`.

#### `SCARA_PROBE_OFFSET_DEGREES`
The angular offset the bed probe is positioned relative to the extruder's nozzle, in degrees. Default is `20` degrees.

**X-SCARA** cant't use the already existing cartesian probe offset configuration in Marlin, because the probe changes orientation when either of the two axis are moving, therefore it also changes the relative position in cartesian space against the extruder's nozzle. This problem only exists in SCARA mechanical models, DELTA, CoreXY and Cartesian printers keep the same X,Y offset of the probe when print head is moving.

To solve this, **X-SCARA** enters in a special `probe` coordinate transformation mode (i.e. `M360 M2`) when required to use the bed probe, applying this offset to the current elbow angle, and instructing the coordinate mapping system to point to the probe, instead of the extruder's nozzle.

Sample configuration that is X-SCARA specific
===
```C
#define SCARA
#define X_SCARA
//#define X_SCARA_DEBUG // activates debug features

#if ENABLED(X_SCARA)

#if ENABLED(X_SCARA)
  // If movement is choppy try lowering this value
  #define SCARA_SEGMENTS_PER_SECOND 30

  // Minimum segment length in mm
  #define SCARA_MIN_SEGMENT_LENGTH  0.5f
  //#define SCARA_FEEDRATE_SCALING

  // Length of inner and outer support arms. Measure arm lengths precisely.
  #define SCARA_LINKAGE_1  98.0    // (mm)
  #define SCARA_LINKAGE_2  98.0    // (mm)
  
  // SCARA tower offset (position of Tower relative to bed zero position)
  #define SCARA_OFFSET_X     0      // (mm)
  #define SCARA_OFFSET_Y    -110    // (mm)

  // Relative probe offset in angles, required for bed leveling (G29)
  #define SCARA_PROBE_OFFSET_DEGREES 20

  // For X-SCARA these are actually degrees not mmm
  // It is useful for homing, to know when the movement exceeds
  // maximum axis length.
  #define X_MAX_LENGTH 300
  #define Y_MAX_LENGTH 300

#endif
#endif
```

Other Marlin configurations
===

Enable saving configuration to EEPROM 
***

I strongly recommend using the EEPROM to save and restore configuration settings.

Otherwise, tuning your machine with `M665` will not allow you to store the resulted values persistently.

```C
/**
 * EEPROM
 *
 * Persistent storage to preserve configurable settings across reboots.
 *
 *   M500 - Store settings to EEPROM.
 *   M501 - Read settings from EEPROM. (i.e., Throw away unsaved changes)
 *   M502 - Revert settings to "factory" defaults. (Follow with M500 to init the EEPROM.)
 */
#define EEPROM_SETTINGS     // Persistent storage with M500 and M501
//#define DISABLE_M503        // Saves ~2700 bytes of PROGMEM. Disable for release!
#define EEPROM_CHITCHAT       // Give feedback on EEPROM commands. Disable to save PROGMEM.
#if ENABLED(EEPROM_SETTINGS)
  //#define EEPROM_AUTO_INIT  // Init EEPROM automatically on any errors.
#endif
```

Centered bed
***

To simplify coordinate mapping **X-SCARA** uses the center of the bed as coordinate origins.
To activate that, enable `BED_CENTER_AT_0_0` in `Configuration.h`.

```C
// The center of the bed is at (X=0, Y=0)
#define BED_CENTER_AT_0_0
```

Bed size
***

In regards of bed size, you can use these settings for safe operation. 

```C
// The size of the print bed
#define X_BED_SIZE 100
#define Y_BED_SIZE 100
```

Steps per unit
===

## X and Y axis
On the **X-SCARA** machine the *X axis* represents the *shoulder joint*, while the *Y axis* represents the *elbow joint*. Therefore, the number of steps per unit describes the number of steps required to move the joint for an angle of 1 degree (unlike the cartesian printers where the unit is 1mm). Depending on the type motors and microstepping configuration you have, the number of steps per degree may differ. 

To speed up your configuration, start from the sample configuration below, wich sets the number of steps for motors having 200 steps/rev and drivers set to 16 microstepping, which is the default for most configurations.

```C
/**
 * X-SCARA: 
 * X - uses 26.6667 steps/degree for moving shoulder (with 16 microsteps)
 * Y - uses 80 steps/degree for moving elbow (with 16 microsteps)
 * Z - uses 400 steps/mm for moving Z (with 16 microsteps)
 * E - adjust according to your extruder (93 is for MK8 extruder)
 */
#define DEFAULT_AXIS_STEPS_PER_UNIT   { 26.6667, 80, 400, 93 }
```

If you increase your microstepping to (let's say) 32, you must double the number of steps for X and Y axis. Same goes if your motors move 400 steps/revolution (0.9 degree per step).

## Generic calculation of steps per unit

If you need the generic formula for calculating the number of steps, this is:

```
shoulder steps  = (shoulder_pulley_teeth / shoulder_motor_pulley_teeth) * number_of_steps_per_revolution / 360

elbow steps     = (elbow_pulley_teeth / elbow_motor_pulley_teeth) * elbow_reduction * number_of_steps_per_revolution / 360

elbow_reduction = elbow_front_pulley_teeth / elbow_back_pulley_teeth
```

In the original design of **X-SCARA** these values are:

Shoulder drive:
* shoulder_pulley_teeth = 60
* shoulder_motor_pulley_teeth = 20

Elbow drive:
* elbow_pulley_teeth = 60
* elbow_motor_pulley_teeth = 20

Elbow reduction:
* elbow_front_pulley_teeth = 60
* elbow_back_pulley_teeth = 20
* elbow_reduction = 3 (60 teeth/20 teeth)

## Let's test the formula:

For a default configuration, having motors with 200 steps per revolution, and 16 microstepping:

```
number_of_steps_per_revolution = 3200 (200 steps per revolution * 16 microstepping)

shoulder steps per unit = 60 / 20 * 3200 / 360      = 9600 / 360 = 26,(6) steps/deg
elbow steps per unit    = 60 / 20 * 3 * 3200 / 360  = 28800 / 360 = 80    steps/deg
```

Or, for example, if you are using 16 teeth pulleys for motors and elbow reduction (instead of 20), motors with 400 steps per revolution, and 32 microstepping, the number of steps will become:

```
number_of_steps_per_revolution = 12800 (400 steps per revolution * 32 microstepping)

shoulder steps per unit = 60 / 16 * 12800 / 360      = 48000 / 360 = 133,(3) steps/deg
elbow steps per unit    = 60 / 16 * 3 * 12800 / 360  = 144000 / 360 = 400    steps/deg
```

## Z and E axis

The Z and E axis are configured similar to any other printer. 

For the Z axis, depending on the lead screw configuration, the formula is:

``` 
Z steps per unit = number_of_steps_per_revolution / lead_screw_mm_per_revolution
```

For the E axis, you need to check your extruder documentation. 

Acceleration and feedrate
***
For the moment, there was no extensive tuning made for this machine to improve print time and travel speed.

The values I use momentarly are to ensure the machine doesn't skip steps and can be increased considerably.

```C

#define DEFAULT_MAX_FEEDRATE          { 300, 300, 15, 30 }
#define DEFAULT_MAX_ACCELERATION      { 1000, 1000, 10, 20000 }

#define DEFAULT_ACCELERATION          1000    // X, Y, Z and E acceleration for printing moves
#define DEFAULT_RETRACT_ACCELERATION  1000    // E acceleration for retracts
#define DEFAULT_TRAVEL_ACCELERATION   1000    // X, Y, Z acceleration for travel (non printing) moves
```

You don't need to modify these values in the configuration file, you may use these as safe settings and tune the machine with `M203` to increase feedrate and `M201` and `M204` to increase acceleration. If the configuration works, save it with `M500` in EEPROM.

Configuration_Adv.h
===
They are no configuration values specific for **X-SCARA** in this file for the moment.

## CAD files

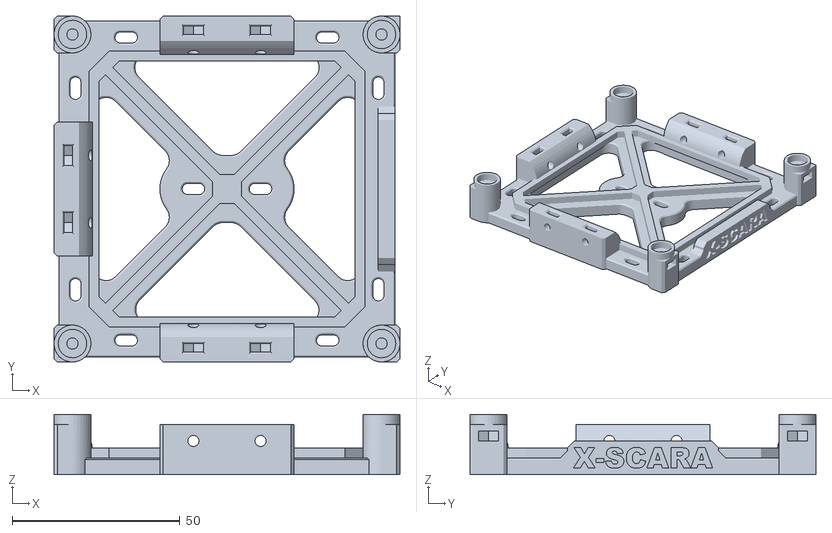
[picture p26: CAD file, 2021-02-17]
hardware/accessories/fixed-bed-mount/STL/Acc_FixedBedMount_HeaterSupport_1.0.5.stl
103.0 x 103.0 x 17.9

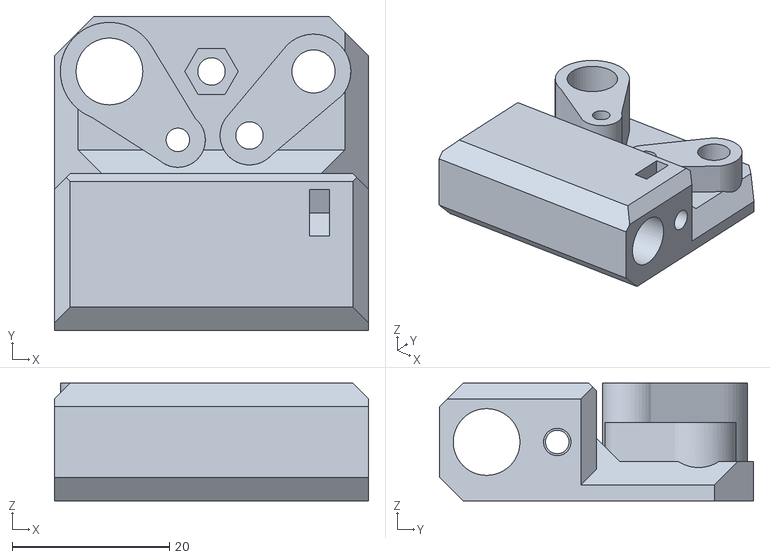
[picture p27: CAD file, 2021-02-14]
hardware/accessories/test-part/Test_hardware_fit_1.0.4.stl
40.0 x 40.0 x 15.0

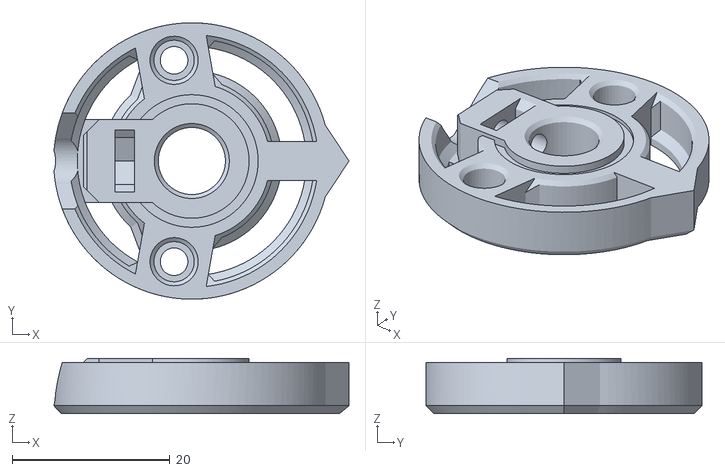
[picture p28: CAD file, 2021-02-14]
hardware/arm/STL/Arm_Endstop_1.0.3.stl
37.4 x 35.0 x 7.00

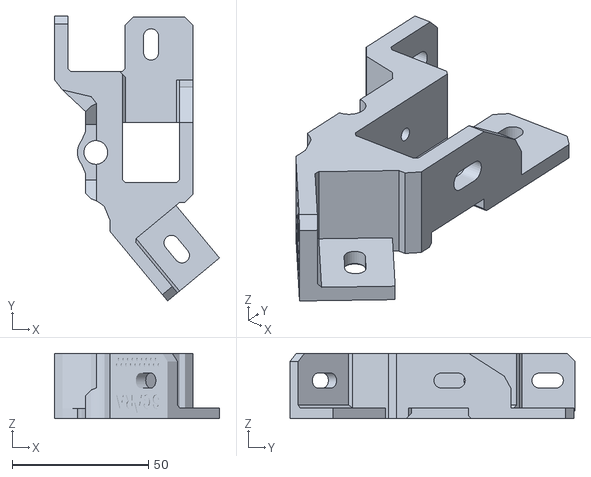
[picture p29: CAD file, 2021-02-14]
hardware/frame/STL/Frame_Plate_Side_Right_1.1.2.stl
60.5 x 104.4 x 24.0

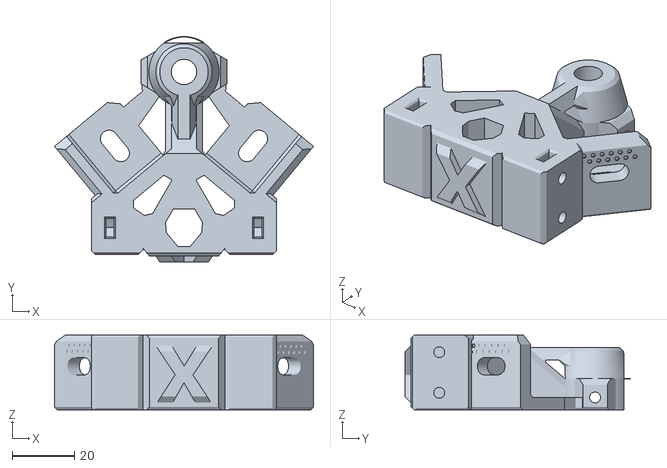
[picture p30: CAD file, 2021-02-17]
hardware/accessories/fixed-bed-mount/STL/Frame_Plate_TipConnector_FixedBedMount_1.0.5.stl
83.0 x 72.3 x 24.0

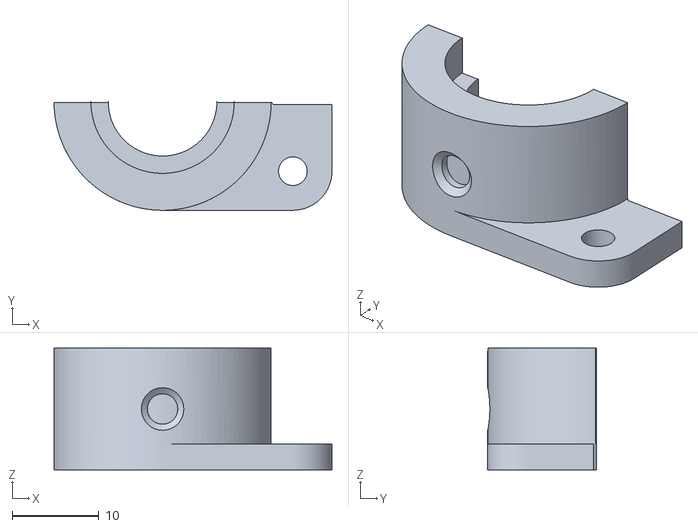
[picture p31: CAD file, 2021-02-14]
hardware/arm/STL/Arm_EMount_Base_Left_1.1.2.stl
32.0 x 12.5 x 14.0

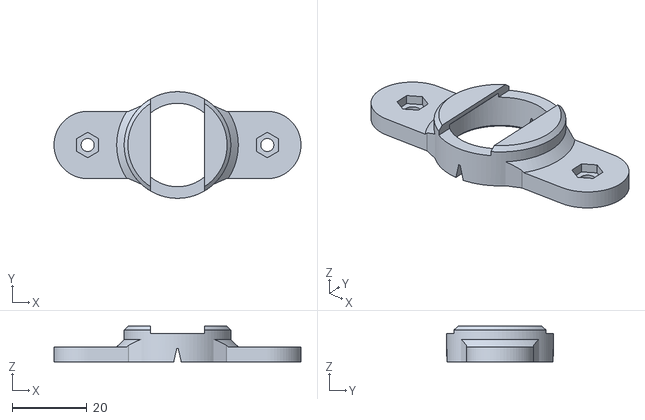
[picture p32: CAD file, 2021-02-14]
hardware/frame/STL/Frame_Z_BearingHolder_1.0.2.stl
66.0 x 28.5 x 9.50

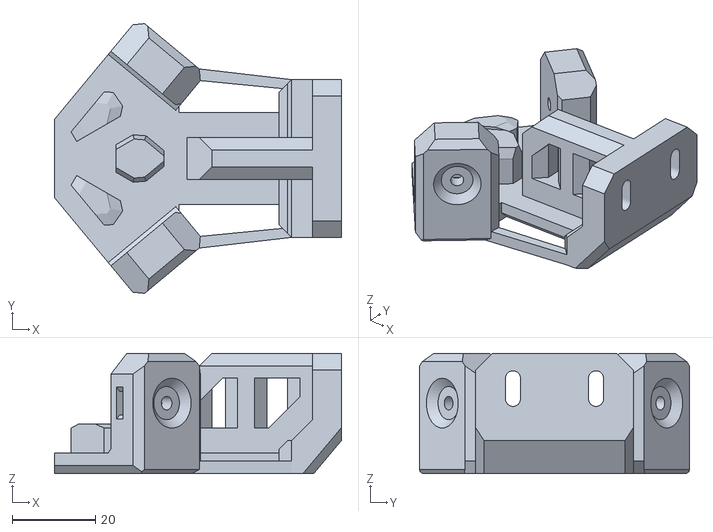
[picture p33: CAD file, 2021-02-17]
hardware/accessories/fixed-bed-mount/STL/Acc_FixedBedMount_AlternativeArm_1.0.5.stl
69.1 x 65.0 x 29.0

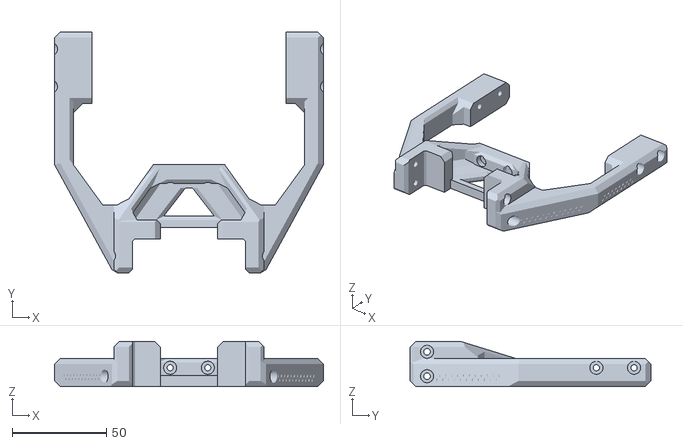
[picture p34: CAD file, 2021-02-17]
hardware/accessories/fixed-bed-mount/STL/Acc_FixedBedMount_Arm_1.0.5.stl
143.0 x 128.1 x 24.0

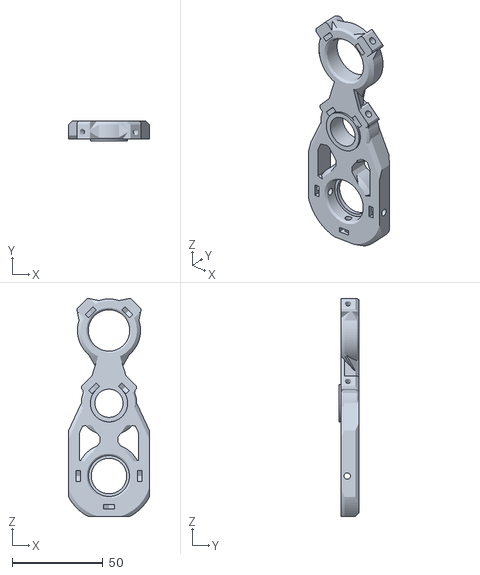
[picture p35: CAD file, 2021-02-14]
hardware/arm/STL/Arm_Shoulder_Connector_1.1.2.stl
44.5 x 11.0 x 119.8

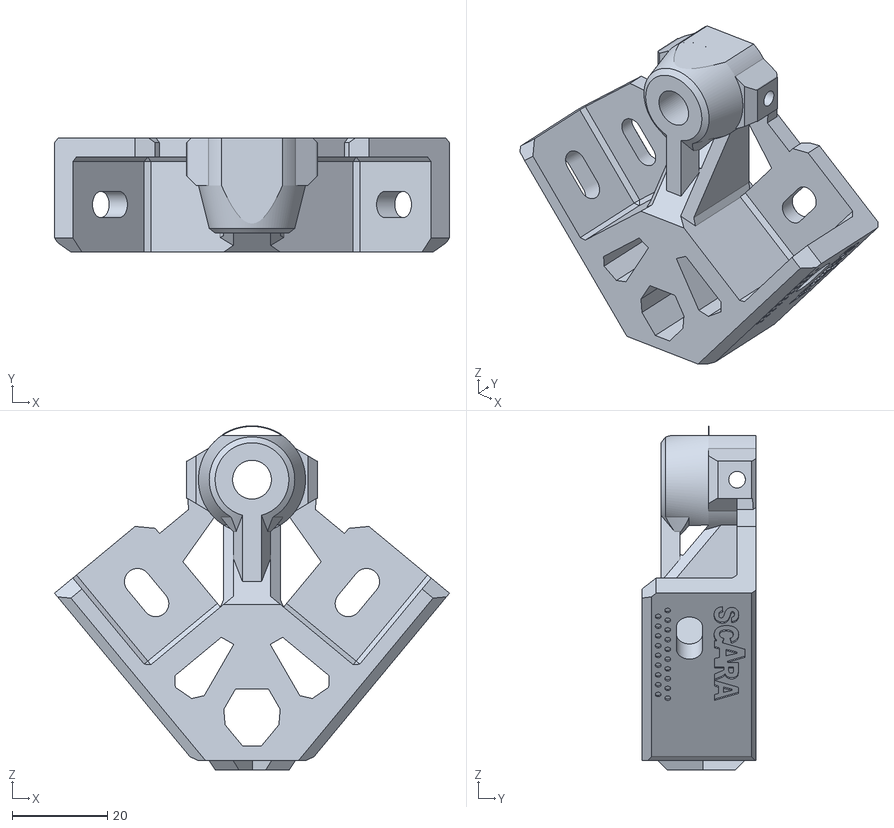
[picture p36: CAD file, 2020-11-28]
hardware/frame/STL/Frame_Plate_TipConnector_1.0.1.stl
83.0 x 24.0 x 72.3

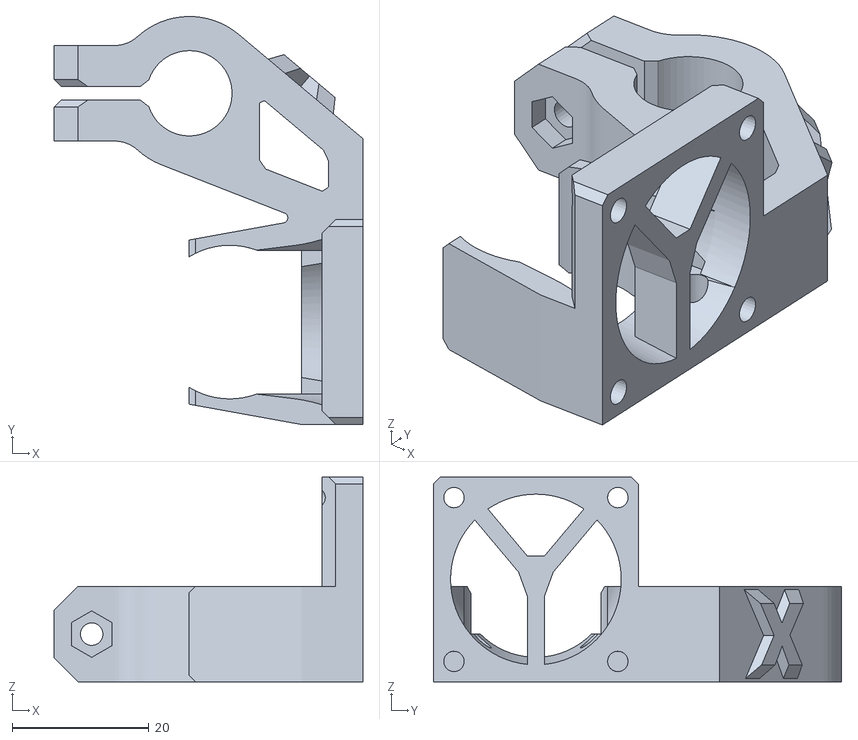
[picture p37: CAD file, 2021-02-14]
hardware/arm/STL/Arm_EMount_Base_ABL_1.1.2.stl
45.2 x 59.8 x 30.0

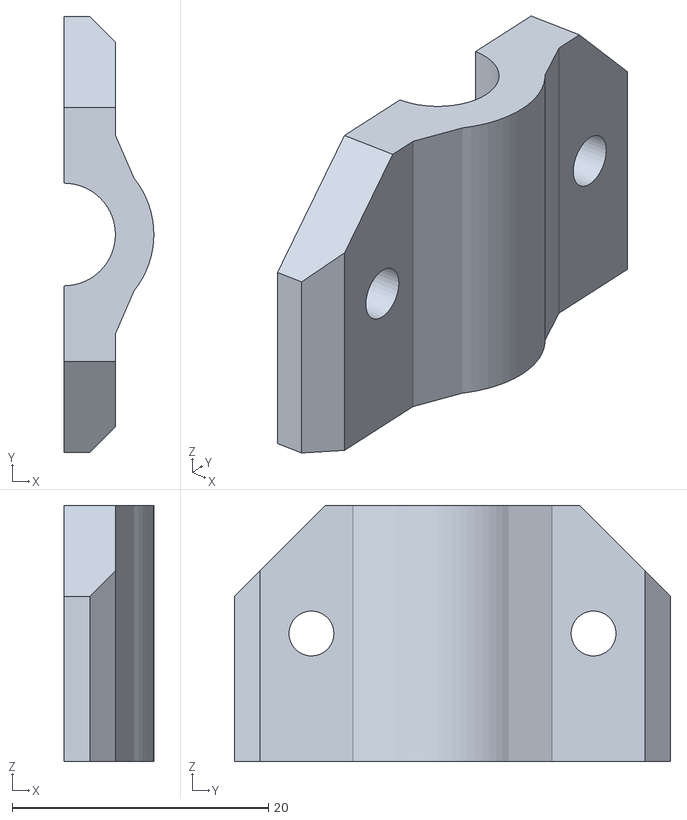
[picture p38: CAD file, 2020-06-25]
hardware/frame/STL/Frame_Plate_Side_RodClamp_1.0.0.stl
7.00 x 34.0 x 20.0

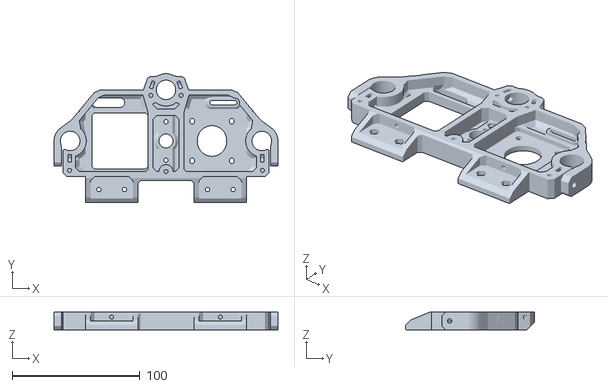
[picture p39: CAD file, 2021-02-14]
hardware/arm/STL/Arm_Base_MotorPlate_1.1.2.stl
175.3 x 100.6 x 14.0

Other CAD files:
hardware/arm/STL/Arm_EMount_Base_Right_1.1.2.stl
hardware/frame/STL/Frame_Plate_Side_Left_1.1.2.stl
hardware/frame/STL/Frame_Z_MotorPlate_1.0.0.stl
hardware/arm/STL/Arm_Base_ZHub_Bottom_1.0.0.stl
hardware/arm/STL/Arm_Base_ZHub_Top_1.0.0.stl
hardware/arm/STL/Arm_Base_ZPlate_Mid_NutHolder_1.0.0.stl
hardware/arm/STL/Arm_Elbow_Plate_Bottom_1.0.0.stl
hardware/arm/STL/Arm_Elbow_Plate_Top_1.0.0.stl
hardware/arm/STL/Arm_Elbow_RodHub_1.0.0.stl
hardware/arm/STL/Arm_Plates_Cover_1.0.0.stl
hardware/arm/STL/Arm_Shoulder_Plate_Bottom_1.0.0.stl
hardware/arm/STL/Arm_Shoulder_Plate_Top_1.0.0.stl
hardware/arm/STL/Arm_SideWall_Left_1.0.0.stl
hardware/arm/STL/Arm_SideWall_Right_1.0.0.stl
hardware/frame/STL/Frame_Z_BearingPlate_1.0.0.stl
hardware/frame/STL/Frame_Z_MotorConnector_1.0.0.stl

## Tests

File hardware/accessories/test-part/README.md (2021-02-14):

X-SCARA test part
===
Print this test part before printing X-SCARA parts.

Hardware Fit
===
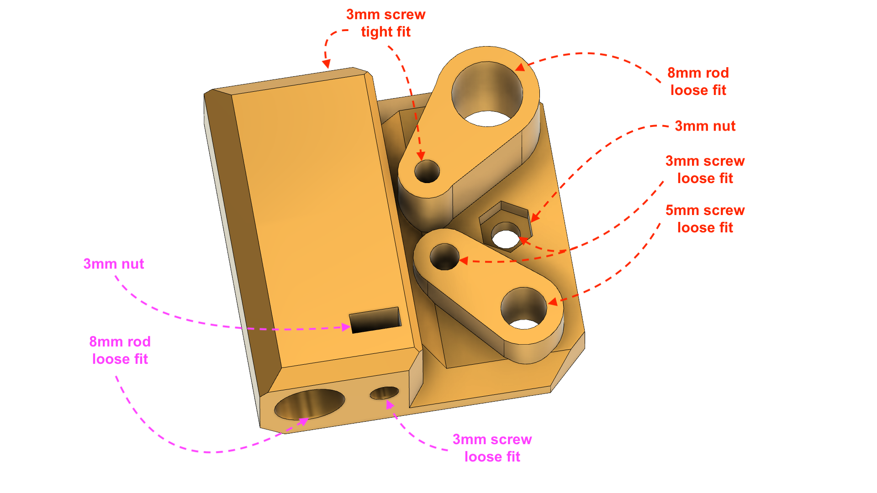
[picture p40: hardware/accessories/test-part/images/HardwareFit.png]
hardware


This part is for testing how the printed parts will fit your hardware.

Follow the above instructions to test how this part fits the M8 rod, M3 screws, M3 nuts and M5 screws. Where is marked *loose fit*, you should be able to pull and push the metal part easily into the part. Where is marked *tight fit* you should be able to screw directly into the plastic part. For the nut, it should fit and stay fixed while screwing tightly.

Tunning
===

X-SCARA parts are designed to have a tolerance to fit precise metal parts. Usually that tolerance is around 0.5 mm.

If your 3D printer is already tuned to accomodate that, you may need to change your settings and let the parts handle the tolerance.

Cura
---

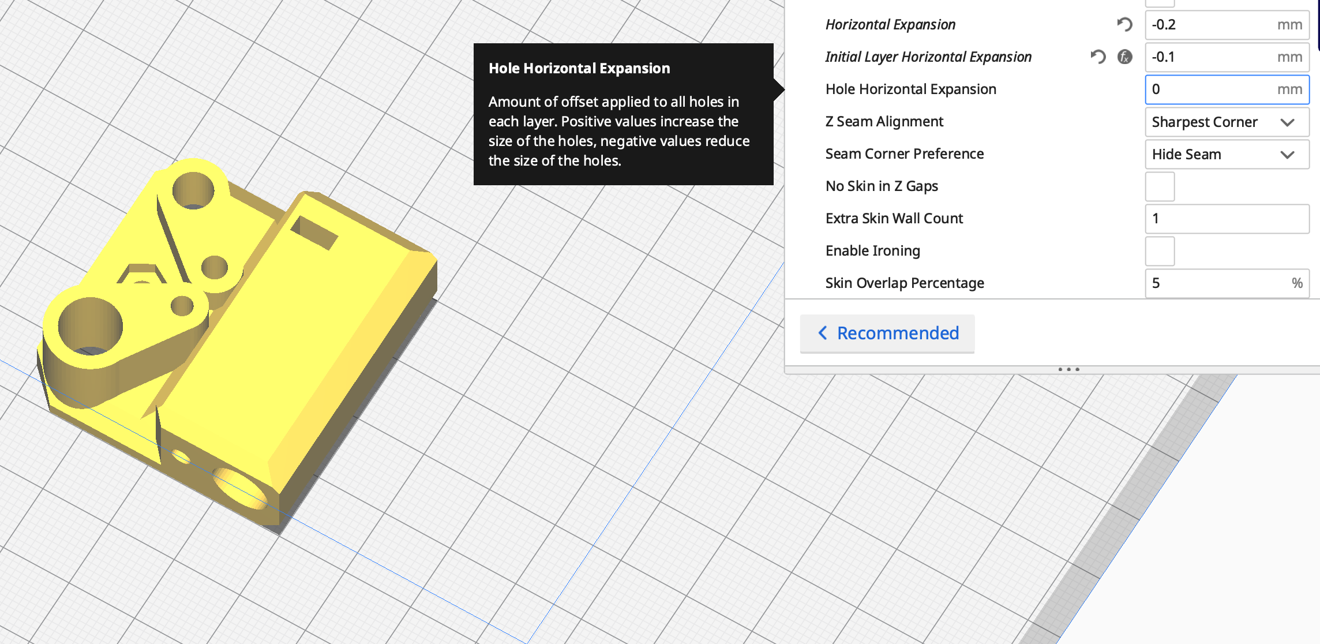
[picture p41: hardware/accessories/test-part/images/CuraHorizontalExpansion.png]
hardware


If your using Cura, one way to tune your profile to print X-SCARA parts correctly, will be to modify the `Shell`->`Hole Horizontal Expansion` and/or `Shell`->`Horizontal Expansion` setting.

These two settings adjust the offset of the inner and outter polygons of your parts. `Horizontal Expansion` usually deals with plastic contraction, so it is usually set it to a small negative values (e.g. -0.2), while `Hole Horizontal Expansion` is for fixing inner perimeters that are too big or too small.

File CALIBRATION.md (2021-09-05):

Calibration
===
> Deprecated for Firmware version 0.4. Soon to be updated.

For the current 0.2 alpha version of the firmware, the machine uses no endstops for the X and Y axis, so calibration must be done manually. The code has been modified so the machine can print and home without endstops, so this will work smoothly.

Step 1 - Set the machine in position
---

If the machine is in arbitrary position, disable motors (`M18`) and move it manully in position.

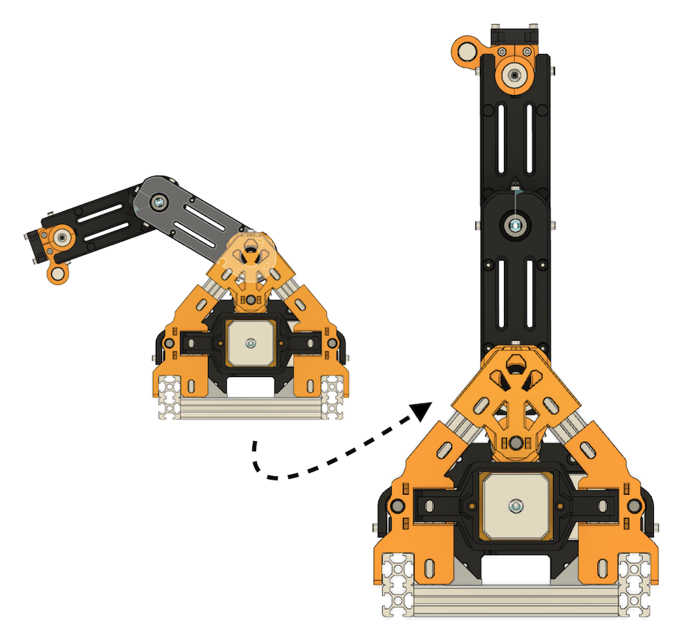
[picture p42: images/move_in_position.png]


You can use these shoulder and elbow screws for reference, to make sure the arm is straight:
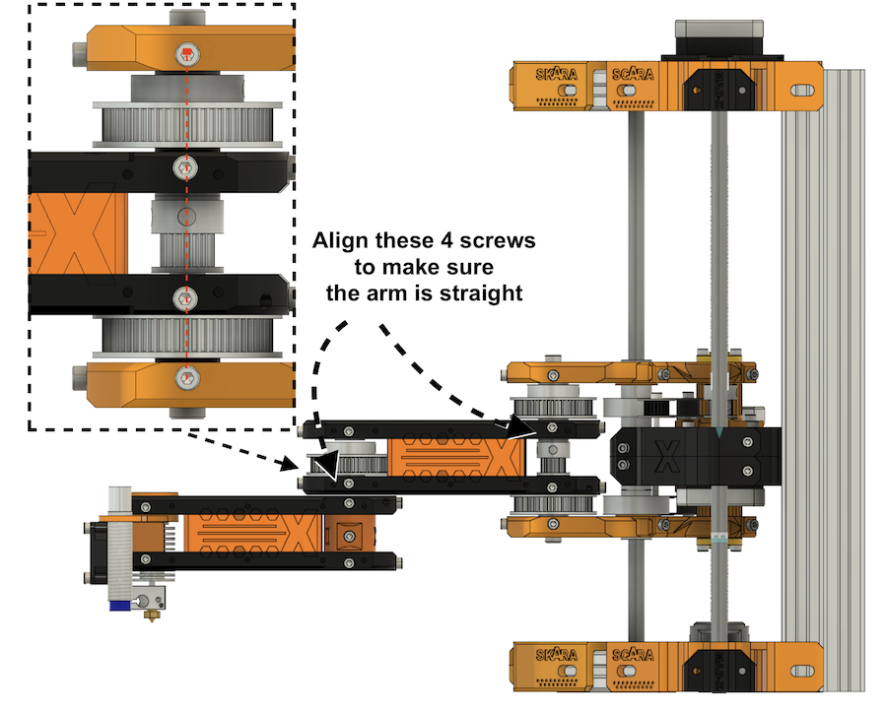
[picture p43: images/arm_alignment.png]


Step 2 - Reset joints angle to 0º
---
Using `M362` set both joints angle to 0º. For more information about `M362` read this [GCodes](firmware/GCODES.md) guide.

```
M362 E0 S0
```

Step 3 - Move to cartesian origin
---
You can now safely move in the cartesian space using `G0` and `G1` commands.

But, before homing, set the machine to its origin. In the default configuration this should coincide with bed center. 

```
G0 X0 Y0
G28
```

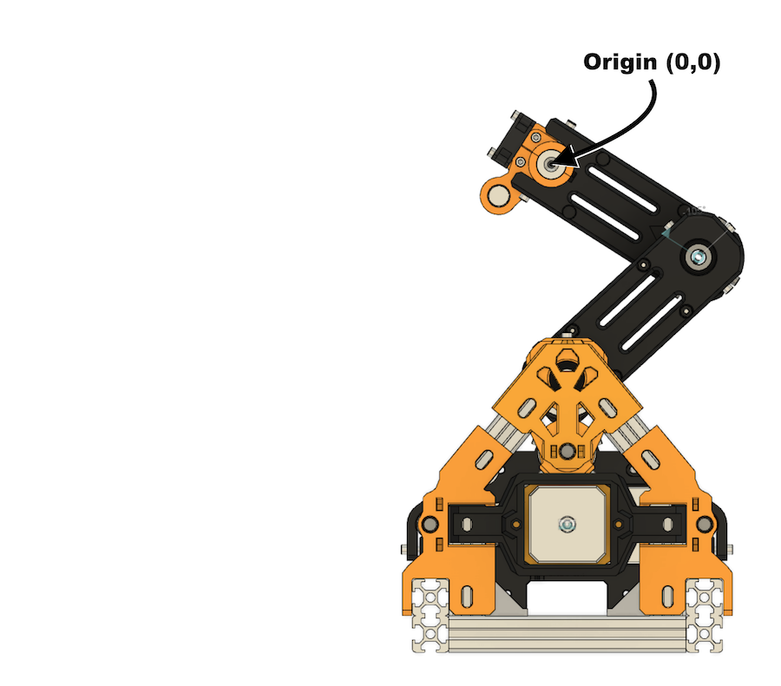
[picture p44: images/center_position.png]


Step 4 - Print
---

You can now home the printer and start printing.

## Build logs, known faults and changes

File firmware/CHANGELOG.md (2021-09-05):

0.1 Alpha
===
- First public release
- Coordinate transformation system ready
- Homing not supported but machine can be manually homed and calibrated with `M362` GCode
- `M360` command for changing coordinate transformation mode from cartesian to angular positioning
- `M361` command for setting joint angles individually, for shoulder and elbow
- `M362` command for setting current position (similar to `G92`)
- `M364` command for getting current X-SCARA version

0.2 Alpha
===
- Inverting X axis direction, parts were printed in mirror

0.3 Alpha
===
- not published

0.4 Beta
===
- Moved to Beta stage: all basic functionality (homing, bed-leveling, EEPROM configuration) implemented & working
- Added coordinate transformation modes to support bed-leveling (`M360 M2` - probe mode)
- Activating `M1` angular coordinate transformation mode automatically on `G28`
- Activating `M2` probe coordinate transformation mode automatically on `G29`
- Implemented homing sequence `G28` (X,Y axis are set as codependent by default, shoulder homes first)
- Modified UBL (Unified Bed Leveling) to support X-SCARA's kinematic model
- Integrated bed-leveling support `G29` (requires `NOZZLE_AS_PROBE` and `SCARA_PROBE_OFFSET_DEGREES` configurations)
- Applying bed leveling for planar moves when bed-leveling is activated
- Modified `M665` for configuring:
    * `M665 D` - number of segments per second for `G1` segmented moves
    * `M665 M` - minimum segment length in mm for segmented moves
    * `M665 X Y` - setting bed center origin relative to shoulder axis (default `SCARA_OFFSET_X` and `SCARA_OFFSET_X`)
    * `M665 E S` - setting home offset in degrees for shoulder and elbow joints (required for precise calibration)
- `M50x` EEPROM commands supported to save, load and reset the values configured with `M665`

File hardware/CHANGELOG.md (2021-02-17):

Versioning scheme
===
Being work in progress, a versioning scheme will is necessary to identify which parts are part of a working set and which not. 
The versioning scheme used is:

    partname_major_minor_revision.STL

  - all parts with the same major version are compatible
  - increasing minor version indicates a change in the part's geometry
  - any estetical changes will not increase the minor version, just the revision
  - revision is incremented within each update on any X-SCARA part

Revision 0
===
- Initial release of X-SCARA frame
- Initial release of X-SCARA mechanics

Revision 1
===
- Typo in part `Frame_Plate_Side_RodClamp_Left`
- Added new frame part mirror `Frame_Plate_Side_RodClamp_Right` which is the mirror version of `Frame_Plate_Side_RodClamp_Left` but without mirrored text
- Corrected extruder mount height

Revision 2
===
- Extruder mount redesigned, probe is now on the left side of the extruder at 20º offset (required by the next version of firmware)
- Updated arm documentation to describe the assembly for the new extruder mount
- Corrected the width of M3 nut holes to be same for all parts, arm and frame (some parts had larger holes for fitting M3 nuts)
- Renamed `Frame_Plate_Side_RodClamp_Left` to `Frame_Plate_Side_Left`
- Renamed `Frame_Plate_Side_RodClamp_Right` to `Frame_Plate_Side_Right`

Revision 3
===
- Added endstop part for holding 5x5 magnets

Revision 4
===
- Added accessory test part [here](accessories/test-part/README.md)

Revision 5
===
- Added accessory for mounting a mini heated bed [here](accessories/fixed-bed-mount/README.md)

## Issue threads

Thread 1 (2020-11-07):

Typos in te arm BOM and numer of print pieces

sl1pkn07, 2020-11-07:
Hi

i've found some typos in the BOM and in the numer of print pieces in the ARM

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

but in the instructions show 2

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

in the BOM sections, show need a 20t(eet) GT2 for 5mm bore

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

but in the instruction, show a 20t FT5 8mm bore
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

this is not expecified in the BOM, for abois missustanding (some kits sell 60t pulleys (8mm bore) + 280mm belts + 20t pulley but with 5mm bore instead of 8mm. i this this need specified in the bom

greetings

sl1pkn07, 2020-11-07:
Hi

also found a missing belt. is the same size like the two others?

greetings

amircescu-gpfw, 2020-11-08:
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

Yes, they are 3 belts in total, all the same length.
Thanks for noticing the BOM problems, I will be fixing them right away.

madl3x, 2020-11-08:
Thanks for noticing the issue. I will verify the BOM and fix it right away.

> also found a missing belt. is the same size like the two others?
Yes, they are 3 and all are 280mm belts.

sl1pkn07, 2020-11-08:
Hi again. durning print, ive found sommeting issues.

the `Arm_Shoulder_Connector`, the screws to fix the bearing arm, seems so be a little more lengeith, 12mm instead of 10mm, because with 10mm the screw is hidde in te piece instead rebase to grip the bearing

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

and in the `Arm_Base_ZHub_Top` and `Arm_Base_ZHub_Bottom`, the holes for the screws not grip the screws. i'm not sure is is a tolerance problem or by design. ive fixing it driling deep the holes and use large screws

greetings

sl1pkn07, 2020-11-08:
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
 K -> C

XD

madl3x, 2020-11-13:
> the `Arm_Shoulder_Connector`, the screws to fix the bearing arm, seems so be a little more lengeith, 12mm instead of 10mm, because with 10mm the screw is hidde in te piece instead rebase to grip the bearing

I checked the design and indeed those are M3 x 12mm not M3 x 10 mm. The documentation for this part wrongly says all screws are M3 x 10 for this part. Front holding the front bearing please use 12 mm screws.

> and in the Arm_Base_ZHub_Top and Arm_Base_ZHub_Bottom, the holes for the screws not grip the screws. i'm not sure is is a tolerance problem or by design. ive fixing it driling deep the holes and use large screws

Are you talking about Z-nut screws that enter the `Arm_Base_Zhub`? Those have a 3.1 mm diameter in design and should hold M3 screws pretty well. If you are slicing with Cura, please check the `Horizontal Expansion` setting. It may help you get the part printed right.

madl3x, 2020-11-13:
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

Yes, correct, please create a different issue for that, so we can easily track each problem.

sl1pkn07, 2020-11-13:
> > the `Arm_Shoulder_Connector`, the screws to fix the bearing arm, seems so be a little more lengeith, 12mm instead of 10mm, because with 10mm the screw is hidde in te piece instead rebase to grip the bearing
>
> I checked the design and indeed those are M3 x 12mm not M3 x 10 mm. The documentation for this part wrongly says all screws are M3 x 10. For holding the front bearing please use M3 x 12 mm screws.

yes. i see that and i fixed in my build

some other pieces need M3x8 instead M3x10

-  for join `Arm_EMount_Fan` to `Arm_EMount_Base_Left `+ `Arm_EMount_Base_ABL`
-  for hold Z Nema17 to pieces
-  for hold the 8x60mm calibrated row to `Arm_Elbow_RodHub` (the screw not thread all, but better than M3x10

and M3x15

-  for hold the  `Arm_Elbow_RodHub` to `Arm_Elbow_Plate`s

the `Arm_Base_MotorPlate` is now in print process

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

the holes should be small than the outter periferic thread of the screw. the drill (normalized, i think) for making M3 threads is 2.5 or 2.25mm/diameter (my thread driver kit have this drill) (https://fullerfasteners.com/tech/recommended-tapping-drill-size/ for example). yes, is possible fix it on the fly with the vertical_expansion (i use superslicer, (from that piece i set 0.1 that value), but i think should be fixed in the STL

> Yes, correct, please create a different issue for that, so we can easily track each problem.

ok

greetings

sl1pkn07, 2020-11-13:
M3x8
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

M3x8 (center) and M3x15
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

sl1pkn07, 2020-11-14:
First `Arm_Base_MotorPlate` printed

-  the screws for grab the nema17 should be M3x8mm (and washer) instead of M3x10
-  if the screws for grab the GT2 idlers is M3, the GT2 idlers should be with bore 3mm instead 5mm. or need make a caps?

greetings

madl3x, 2020-11-21:
> * the screws for grab the nema17 should be M3x8mm (and washer) instead of M3x10
I'll keep that in mind but mostly depends on the motor you have. Some NEMA17 motors have deeper threads for screws. The `Arm_Base_MotorPlate` part is 4 mm thick where it connects with the motor and therefore 6mm from the screw's thread will go into the motor itself. But some motors may not accommodate that.

> if the screws for grab the GT2 idlers is M3, the GT2 idlers should be with bore 3mm instead 5mm. or need make a caps?
That is another good remark. The GT2 idlers I used are 3mm ID, not 5mm inner bore like the BOM says. I will correct that and close this issue when I fix the BOM.

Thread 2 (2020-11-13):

E3D hotend support not fit in the elbow top/bottom plates

sl1pkn07, 2020-11-13:
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

madl3x, 2020-11-13:
Thank you, your reported issue is correct. There is an overlap of 1.61 mm between the parts.
I will fix it and update the STL and .f3d files. Until then please just trim your part or cut the STL with an editor, so you can finish the assembly.

sl1pkn07, 2020-11-13:
thanks, but i don't have hurry at all, the frame prefix and the most mechanic parts is still on transit (ETA end of november or start of december)

so take you time

greetings

Closed 2020-11-28.

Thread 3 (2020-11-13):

Typo in the Frame_Plate_SideConnector piece

sl1pkn07, 2020-11-13:
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
 K -> C

greetings

sl1pkn07, 2020-11-21:
Hi

for print this piece, in the right side, is needed to print it in mirror mode, but the text is also morrored

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

for look&feel better, i think this piede needs to be added in the piece list a mirrored piece but with thext in the rigth position

what you think?

greetings

madl3x, 2020-11-28:
Fixed typo. Added two separate versions (left and right) for the side connectors. Thank you for noticing.

Closed 2020-11-28.

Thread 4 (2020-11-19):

[INFO] Electronics, Endstops and Marlin, How do it

sl1pkn07, 2020-11-19:
Hi, my setup is almst done (missing frame pieces), but i can adapt the ectronics to the machine

what is the minimun requirements (inputs/outputs) for this project?, (a Fysetc AIOII https://github.com/FYSETC/FYSETC-AIO_II is sufficient? (with TMC2208, Silent, but no sensorless :( )

where i can set the axis endstops in the machine? can you share you endstops mounts? (i see something in the instagram vids, but i'm not clear)

in marlin (2.0.x) exist config for SCARA machines, one is `MP_SCARA`, and other is `Morgan_SCARA`, what is the best fit for this machine?

greetingsd

madl3x, 2020-11-21:
Hello,

Endstops is the last missing piece of this machine and that was what I was working on. Current design is missing that. Technically speaking, you can use normal mechanical endstops and mount them on Arm Base part like all the other SCARA models do. That's how both Morgan and MP Scara works as well.

My design (what you've seen in the Instagram videos) uses something else. It's a center magnetical endstop-like device which Marlin does not support yet. The "endstop" serves as a sensor which tells the machine where the arm shoulder and arm elbow are fully extended (i.e. the angle they make relative to machine's front axis  is 0º). This is not yet implemented in Marlin and I've worked on that but not fully finished. I need to rewrite the home sequence (G28) to make that work.

Untill then, you can use mechanical endstops connected to the Arm Base part.

Regarding which model to use (Morgan or MP_SCARA), I started from Morgan Scara but rewrited the inverse kinematics code for that to work. I have that completed already and I will post an update with an Alpha firmware to have access to the code, soon. This will make your machine move in the X,Y cartesian space correctly.

sl1pkn07, 2020-11-29:
Hi. my printer is almost done

i have used the marlin Morgan configuration adapted to my board, and need apply (bugfix-2.0.x) this patchs

https://github.com/annhan/Configurations/commit/1c23a536228de459c9f6fc3cb4811e3a498e3bba
https://github.com/MarlinFirmware/Marlin/pull/17274

but not work at all (only home X and Y, the rest fails)

i use Hall effect Endstops (KY-003) fixed (with little screws) the Arm_SideWall pieces in the Elbow and Shoulder, activated with little neodimium magnets (one fixed in the Arm_Base_MotorPlate, and other in the bottom Arm_Shoulder_Connector). this works as spected

question. what mean "THETA" and "PSI" in this environment?

greetings

sl1pkn07, 2020-11-29:
[VID_20201129_224254.zip](https://github.com/madl3x/x-scara/files/5612902/VID_20201129_224254.zip) (rename to 3gp)
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

madl3x, 2021-01-15:
@sl1pkn07 You might wanna take a look at the first firmware release I made.
https://github.com/madl3x/x-scara/tree/master/firmware

Version 0.1 works without X,Y endstops (for the moment), with manual calibration (use M362, check the Gcodes guide I've published). I am going to release 0.2 soon (fixes the orientation of the cartesian space) and after that, I will implement homing, end-stops mounting and bed leveling.

I just ordered the same endstops you have, and got the package today, so I will be able to work on that soon. I like your positioning but I have another idea in mind. Keep you posted.

sl1pkn07, 2021-01-15:
the positionn is reversed. my phone break that day and i take the photos with the tablet frontal cam

amircescu-gpfw, 2021-01-15:
Off-topic: @sl1pkn07 please post a make on thingiverse, if your machine is ready. I would love to see more pictures of it and in more detail.
On-topic: I will get back to endstops after i make this second update on the firmware.

sl1pkn07, 2021-01-17:
Hi

i've apply you changes for Xscara (based in marlin 2.5.0.2(?)) to upstream marlin bugfix-2.0.x branch

steps i do:

- download you repo
- download marlin by git point to 2.0.5.2 tag
- copy you marlin to cloned upstream marlin
- review the changes
- git diff > patch.patch
- revert the changes and checkout to bugfix-2.0.x branch
- apply the patch created before
- fix the rejected code and review again

~~~patch
diff --git a/.gitignore b/.gitignore
index 62f73a7c0d..88286ebe5d 100755
--- a/.gitignore
+++ b/.gitignore
@@ -23,6 +23,9 @@
 # NEVER put it in the repository
 _Version.h

+process-palette.json
+.pio/
+
 #
 # OS
 #
diff --git a/Marlin/src/core/language.h b/Marlin/src/core/language.h
index d6048d293c..af3ee3479d 100644
--- a/Marlin/src/core/language.h
+++ b/Marlin/src/core/language.h
@@ -126,7 +126,11 @@
 #define STR_E_STEPPER_NOT_SPECIFIED         "E stepper not specified"
 #define STR_INVALID_SOLENOID                "Invalid solenoid"
 #define STR_COUNT_X                         " Count X:"
+#if ENABLED(X_SCARA)
+#define STR_COUNT_A                         "\nMotors A:"
+#else
 #define STR_COUNT_A                         " Count A:"
+#endif
 #define STR_WATCHDOG_FIRED                  "Watchdog timeout. Reset required."
 #define STR_ERR_KILLED                      "Printer halted. kill() called!"
 #define STR_ERR_STOPPED                     "Printer stopped due to errors. Fix the error and use M999 to restart. (Temperature is reset. Set it after restarting)"
diff --git a/Marlin/src/gcode/calibrate/M665.cpp b/Marlin/src/gcode/calibrate/M665.cpp
index 557204cc11..a13552fa30 100644
--- a/Marlin/src/gcode/calibrate/M665.cpp
+++ b/Marlin/src/gcode/calibrate/M665.cpp
@@ -62,6 +62,31 @@

   #include "../../module/scara.h"

+  #if ENABLED(X_SCARA)
+  /**
+   * M665: Set SCARA settings
+   *
+   * Parameters:
+   *
+   * D<bool> - debug on or off (if compiled with X_SCARA_DEBUG)
+   * S<int>  - number of segments per second
+   */
+  void GcodeSuite::M665() {
+
+    #if ENABLED(X_SCARA_DEBUG)
+      if (parser.seenval('D')) {
+        x_scara_debug = parser.value_bool();
+      }
+      SERIAL_ECHOPAIR("Debug:", x_scara_debug, " ");
+    #endif
+
+    if (parser.seenval('S')) delta_segments_per_second = parser.value_float();
+
+    SERIAL_ECHOLNPAIR("Seg/Sec:", delta_segments_per_second);
+  }
+
+  #else // X_SCARA
+
   /**
    * M665: Set SCARA settings
    *
@@ -107,6 +132,6 @@
     #endif // HAS_SCARA_OFFSET
   }

-#endif
-
+#endif // MORGAN_SCARA or MP_SCARA
+#endif // IS_SCARA
 #endif // IS_KINEMATIC
diff --git a/Marlin/src/gcode/gcode.cpp b/Marlin/src/gcode/gcode.cpp
index 89bc0dc7af..8b289f59b8 100644
--- a/Marlin/src/gcode/gcode.cpp
+++ b/Marlin/src/gcode/gcode.cpp
@@ -691,6 +691,14 @@ void GcodeSuite::process_parsed_command(const bool no_ok/*=false*/) {
         case 364: if (M364()) return; break;                      // M364: SCARA Psi pos3 (90 deg to Theta)
       #endif

+      #if ENABLED(X_SCARA)
+        case 360: M360(); break;                                  // M360: X-SCARA Change coordinate transformation mode
+        case 361: M361(); break;                                  // M361: X-SCARA Move joints to position
+        case 362: M362(); break;                                  // M362: X-SCARA Set current joints position
+        case 363: M363(); break;                                  // M363: X-SCARA Configure
+        case 364: M364(); break;                                  // M364: X-SCARA Get version
+      #endif
+
       #if EITHER(EXT_SOLENOID, MANUAL_SOLENOID_CONTROL)
         case 380: M380(); break;                                  // M380: Activate solenoid on active (or specified) extruder
         case 381: M381(); break;                                  // M381: Disable all solenoids or, if MANUAL_SOLENOID_CONTROL, active (or specified) solenoid
@@ -789,7 +797,7 @@ void GcodeSuite::process_parsed_command(const bool no_ok/*=false*/) {
         case 605: M605(); break;                                  // M605: Set Dual X Carriage movement mode
       #endif

-      #if ENABLED(DELTA)
+      #if ENABLED(DELTA) || ENABLED(IS_SCARA)
         case 665: M665(); break;                                  // M665: Set delta configurations
       #endif

diff --git a/Marlin/src/gcode/gcode.h b/Marlin/src/gcode/gcode.h
index 735456a533..d50e501cf5 100644
--- a/Marlin/src/gcode/gcode.h
+++ b/Marlin/src/gcode/gcode.h
@@ -275,12 +275,15 @@
  * M951 - Set Magnetic Parking Extruder parameters. (Requires MAGNETIC_PARKING_EXTRUDER)
  * M7219 - Control Max7219 Matrix LEDs. (Requires MAX7219_GCODE)
  *
+ * For MORGAN_SCARA and MP_SCARA
  * M360 - SCARA calibration: Move to cal-position ThetaA (0 deg calibration)
  * M361 - SCARA calibration: Move to cal-position ThetaB (90 deg calibration - steps per degree)
  * M362 - SCARA calibration: Move to cal-position PsiA (0 deg calibration)
  * M363 - SCARA calibration: Move to cal-position PsiB (90 deg calibration - steps per degree)
  * M364 - SCARA calibration: Move to cal-position PSIC (90 deg to Theta calibration position)
  *
+ * For X_SCARA
+ *
  * ************ Custom codes - This can change to suit future G-code regulations
  * G425 - Calibrate using a conductive object. (Requires CALIBRATION_GCODE)
  * M928 - Start SD logging: "M928 filename.gco". Stop with M29. (Requires SDSUPPORT)
@@ -724,6 +727,14 @@ private:
     static bool M364();
   #endif

+  #if ENABLED(X_SCARA)
+    static void M360();
+    static void M361();
+    static void M362();
+    static void M363();
+    static void M364();
+  #endif
+
   #if EITHER(EXT_SOLENOID, MANUAL_SOLENOID_CONTROL)
     static void M380();
     static void M381();
diff --git a/Marlin/src/gcode/geometry/G92.cpp b/Marlin/src/gcode/geometry/G92.cpp
index 1a0382ed7c..b211fbec99 100644
--- a/Marlin/src/gcode/geometry/G92.cpp
+++ b/Marlin/src/gcode/geometry/G92.cpp
@@ -28,6 +28,10 @@
   #include "../../feature/encoder_i2c.h"
 #endif

+#if ENABLED(X_SCARA)
+  #include "../../module/scara.h"
+#endif
+
 /**
  * G92: Set current position to given X Y Z E
  */
diff --git a/Marlin/src/gcode/geometry/M206_M428.cpp b/Marlin/src/gcode/geometry/M206_M428.cpp
index efb89fbcf2..fc7ce0ea98 100644
--- a/Marlin/src/gcode/geometry/M206_M428.cpp
+++ b/Marlin/src/gcode/geometry/M206_M428.cpp
@@ -48,7 +48,7 @@ void GcodeSuite::M206() {
     if (parser.seen(XYZ_CHAR(i)))
       set_home_offset((AxisEnum)i, parser.value_linear_units());

-  #if ENABLED(MORGAN_SCARA)
+  #if ENABLED(IS_SCARA)
     if (parser.seen('T')) set_home_offset(A_AXIS, parser.value_float()); // Theta
     if (parser.seen('P')) set_home_offset(B_AXIS, parser.value_float()); // Psi
   #endif
diff --git a/Marlin/src/gcode/scara/M360-M364.cpp b/Marlin/src/gcode/scara/M360-M364.cpp
index 562beee4f9..2f2fa4456f 100644
--- a/Marlin/src/gcode/scara/M360-M364.cpp
+++ b/Marlin/src/gcode/scara/M360-M364.cpp
@@ -29,53 +29,179 @@
 #include "../../module/motion.h"
 #include "../../MarlinCore.h" // for IsRunning()

-inline bool SCARA_move_to_cal(const uint8_t delta_a, const uint8_t delta_b) {
-  if (IsRunning()) {
-    forward_kinematics_SCARA(delta_a, delta_b);
-    do_blocking_move_to_xy(cartes);
+  // TODO: fix morgan scara
+#elif ENABLED(X_SCARA)
+
+#include "../gcode.h"
+#include "../../module/scara.h"
+#include "../../module/motion.h"
+#include "../../module/planner.h"
+#include "../../MarlinCore.h" // for isRunning()
+
+FORCE_INLINE static bool _check_if_running() {
+  if (!IsRunning()) {
+    SERIAL_ECHOLNPGM("X-Scara is not running!");
     return true;
   }
   return false;
 }
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

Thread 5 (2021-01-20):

Missing download button!

alassedy, 2021-01-20:
Hi,
I tried to download the Fusion 360 version of your design, but I couldn't find the download button for the arm assembly when opened this link:
https://a360.co/2YkuguU
Unlike the frame assembly like which has the download button.
Thank you for the great design.

madl3x, 2021-01-31:
I'll verify that, but you can download the STLs from Github or Thingiverse. Check out the releases section.

jschilli, 2022-12-11:
is it possible to allow downloads of the arm models?  The 'allow item to be downloaded' switch needs to be on in Fusion when sharing the link.

I'm looking to model new end effectors on the arm and it would be helpful to evolve your model vs starting from scratch.

Great project!

Closed 2021-09-05.

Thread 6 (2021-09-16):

Electronics BOM

vojjta, 2021-09-16:
Hi, I really like this project and I want to build it. But in documentation is missing electronics BOM. For example what endstops are used? I know that hall effect sensors but what type, how they are placed... Thank you

madl3x, 2021-09-16:
Hello,

Yes, you are right, I should do an electronics BOM.

Untill then, check out this page:
https://github.com/madl3x/x-scara/tree/master/hardware/arm

This picture to be more specific:
[image: image.png]

I used magnetic endstops and a mount that holds 5x5 mm cylindrical magnets.

This one should work fine:
https://www.my-home-fab.de/en/reprap-3d-hardware/electronics/51/rrd-hall-endstop

You can find other types of magnetic endstops, or you can even make your
own.
If you want to use optical endtsops, you can use them, but you have to
redesign the part that is coupled with the rod, to act as a flag that goes
in the optical sensor.

Regards,
Alex M.

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

vojjta, 2021-09-18:
Thank you for your answer.

This one should be also ok?
[Hall magnetic Sensor with analog & digital outs](https://www.aliexpress.com/item/32653988546.html?spm=a2g0o.cart.0.0.3d4a3c00v27LKX&mp=1)

madl3x, 2021-09-18:
It's too long. It will probably fit on top of the arm, but it will not fit on the shoulder joint.
This RADDS Hall-Effect could be a second option:
https://reprapworld.eu/electronics/endstops/hall_e_endstop/#description

You can find suppliers for this one all around the world.

sl1pkn07, 2021-10-18:
if help, my hall units comes from here https://www.ebay.es/itm/221805903273?hash=item33a4a97da9:g:a3cAAOSwnw9Z90Wh (is a local store on my country, no from china (i mean, the delivery)). something similar should be exist in your country (for examplem, from DE https://www.ebay.de/itm/152368482760?hash=item2379de89c8:g:PqQAAOSwOQJeagV8)

greetings

iamthebest22, 2021-11-20:
Sorry for the late question, would this one work? As the RADDS one is out of stock at my location?
https://spool3d.ca/hall-sensor-module-endstop/

amircescu-gpfw, 2021-12-02:
> Sorry for the late question, would this one work? As the RADDS one is out of stock at my location? https://spool3d.ca/hall-sensor-module-endstop/

Yes, it would work. Actually it's the same with the one that I am using.

iamthebest22, 2021-12-02:
Thanks! Now let's hope the newest version of Marlin can do SCARA with his settings fine. I just had to change X-scara to MP_Scara

iamthebest22, 2021-12-05:
> > Sorry for the late question, would this one work? As the RADDS one is out of stock at my location? https://spool3d.ca/hall-sensor-module-endstop/
>
> Yes, it would work. Actually it's the same with the one that I am using.

nice, how did you mount it? Since it uses two M2 screws, I am not quite sure how to mount it on the elbow one. is there a picture you could show me?

madl3x, 2021-12-05:
Sure check [this pic](https://photos.google.com/share/AF1QipNQx_2L8vYkozSCluqT0DdA4VPUnM8ntkQr1BmR7Fuyo9QzZPlhhxQG7TyLyEseVw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) and [this one](https://photos.google.com/share/AF1QipP8QMgJ6HX2Ko4WXrdBte_jJvhIJaoFje7oFavgWGwPmNMKQPuTCMILyECJUM7MMA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).

I used a strong double adhesive tape along with a tie wrap.
After the adhesive hardens the tie wrap is pretty much redundant.

iamthebest22, 2021-12-06:
Ohhh that one nice. I should be more clear, I meant the other arm, the one where there's less space. Currently I drilled a small M2 hole and used hot glue, and seems to be well, but would definitely like to see wha tyou use.

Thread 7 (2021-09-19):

BOM

vojjta, 2021-09-19:
Hi,

I went through BOM and there are probably some small mistakes.

In [Arm](https://github.com/madl3x/x-scara/blob/master/hardware/arm/README.md) is Tr8 Z-Nut and in [Frame](https://github.com/madl3x/x-scara/blob/master/hardware/frame/README.md) is T-Nuts. Are those same nuts for lead screw?

In [Frame](https://github.com/madl3x/x-scara/blob/master/hardware/frame/README.md) is 4 pieces for 20x20 60mm aluminum profile. But should not it be 8 pieces(4 for bottom and 4 for top part of frame)?

I am preparing [Sourcing guide](https://docs.google.com/spreadsheets/d/17AkOFRG1sNOwA-htXEAFYQWag8pyb9Ng2faQ-IcJ8a0/edit?usp=sharing) for my self... Would it help also to your project?

madl3x, 2021-09-19:
The Z-nut is [this one](https://www.geeetech.com/images/l/Geeetech_nut.jpg) and the is nut connecting the lead screw to the motor plate.
T-nuts are for frame assembly and they look [like this](https://www.norelem.com/xs_db/BILD_DB/0/www/750/07090.jpg). They are a bit expensive, so for 20x20 aluminum profiles, you can also use square M5 nuts.

```In Frame is 4 pieces for 20x20 60mm aluminum profile. But should not it be 8 pieces(4 for bottom and 4 for top part of frame)?```
That is correct, I will fix that.

```I am preparing Sourcing guide for my self... Would it help also to your project?```
Sure. Let me know when you're done and I will take a look.
It would be good to be in text format, so it can be tracked by git.

madl3x, 2021-09-19:
Fixed with commit 995abc5.

vojjta, 2021-09-20:
>The Z-nut is this one and is the nut connecting the lead screw to the motor plate.
T-nuts are for frame assembly and they look like this. They are a bit expensive, so for 20x20 aluminum profiles, you can also use square M5 nuts.

As a second point in "Screws and nuts" for frame is 50 x M5 Drop In Hammer T-Nuts for 2020 (OR 50 x M5 square Nuts for 2020) and as a last one is 2 x T-Nuts (corresponding to your chosen lead screw). For Arm in section  "Screws and nuts" is 2 x Tr8 Z-Nut (1 is mandatory, 2 are optional). That is whay I think, that nut for lead screw is mentioned twice

Closed 2021-09-19.

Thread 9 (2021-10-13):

Calibration problem

tsogoo, 2021-10-13:
Hi. I created scara and configured:
```
  // Length of inner and outer support arms. Measure arm lengths precisely.
  #define SCARA_LINKAGE_1  135.0    // (mm)
  #define SCARA_LINKAGE_2  125.0    // (mm)

  // SCARA tower offset (position of Tower relative to bed zero position)
  #define SCARA_OFFSET_X     0      // (mm)
```
I approximated :
```
  #define SCARA_OFFSET_Y    -148    // (mm) I approximated it
```
Configured for my gears:
```
  #define DEFAULT_AXIS_STEPS_PER_UNIT   { 46, 40, 400, 418.5 } // For my printers gears
```

Then when I command `M361 S0 E90` Elbow moves 90 degrees
when I command `M361 S45 E0` Shoulder moves 45 degrees but elbow degree around 30 to 40. Is it ok? If not what it should be?

And sent gcode to draw circle but it draws egg shape.

tsogoo, 2021-10-13:
When I command `M361 S45 E0` or `M361 S90 E0` elbow doesn't go 0 degrees. and elbow stepper motor moves.

madl3x, 2021-10-14:
From what I see in the pictures, your model has no mechanical crosstalk between elbow and shoulder, and X-scara does.
X-scara shares with the shounder the elbow reduction gear, which influences the elbow's movement when the shoulder moves.

Try patching `Marlin/src/module/scara.cpp`, and replace lines 339-375 with this:

```C
/* forward kinematics transformation */
static  FORCE_INLINE void x_scara_fwdk(const float &a, const float &b) {
    const float S = a;
    const float E = b-a; // removing crosstalk (/3)

    const float a_sin = - sin(RADIANS(S)) * L1,
                a_cos =   cos(RADIANS(S)) * L1,
                b_sin = - sin(RADIANS(S+E)) * L2,
                b_cos =   cos(RADIANS(S+E)) * L2;

    cartes.set(a_sin + b_sin + scara_offset.x,
               a_cos + b_cos + scara_offset.y);

    X_SCARA_DEBUG_LNPAIR(
      "FWDK S:", S," E:", E," -> X:", cartes.x," Y:", cartes.y);
}

/*  inverse kinematics transformation */
static FORCE_INLINE void x_scara_invk(const xyz_pos_t &raw) {

    const float x = - (raw.x - scara_offset.x);
    const float y =   (raw.y - scara_offset.y);

    float x2y2 = sq(x) + sq(y);
    float hypot = SQRT(x2y2);

    if(hypot == 0) hypot = 0.000001; // avoid division by zero

    float S = ATAN2(x,y) - ACOS((x2y2 + PK_DifLenSqrd )/(2*L1*hypot));
    float E =              ACOS((x2y2 - PK_SumLenSq   )/(PK_ProdOfLen)) + S; // removing crosstalk (/3)

    delta.set(DEGREES(S), DEGREES(E), raw.z);

    X_SCARA_DEBUG_LNPAIR(
      "INVK X:",raw.x," Y:", raw.y, " -> S:", DEGREES(S)," E:", DEGREES(E));
}
```

tsogoo, 2021-10-25:
So I can choose `SCARA_OFFSET_Y` in specific range. It doesn't effect to drawing shape (circle to ellipse). right?
Maybe perfect elbow angle (SCARA_OFFSET_Y value) to increase quality, right?

I have also one problem. I fixed drawing egg problem. But now I have an ellipse issue. I think I configured arm lengths correct.
And my models shoulder, elbow arm goes right angles (Goes 90 degrees approximately, I used formula but didn't go 90 degree correctly. So I had to use command `M92 X Y` to calibrate angles.).

ToonKru3, 2022-03-09:
i have i same problem have here when i calibrate  move stright manually and then `M362 E0 S0` and `G0 X0 Y0` and i try test move x and y button by Repetier-Host is curve shape to trapezoid

ToonKru3, 2022-03-09:
Can you re-write step by step for calibrate abotu how to fix trapazoid. I have followed by your instruction but it's trapzoid (square shape) and oval (circle shape)

ToonKru3, 2022-03-09:
or some much detail video about how to set up step by step

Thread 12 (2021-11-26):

Board not in the beta firmware, so having issues

iamthebest22, 2021-11-26:
I'll try my best to explain this, the beta firmware you've provided, unless I've missed something, doesn't have the BigTreeTech 32 bit SKR V2.0 board, so I had to download the newest 2.0.9.2 marlin firmware, and then made changes. some of the errors that it gave me before I changed it to "fix" them were like

"SCARA is now Morgan_scara"

so what do now do now? This works, but I'm pretty sure is not what you've meant. Thanks

iamthebest22, 2021-11-26:
Here is the whole configuration.h
/**
 * Marlin 3D Printer Firmware
 * Copyright (c) 2020 MarlinFirmware [https://github.com/MarlinFirmware/Marlin]
 *
 * Based on Sprinter and grbl.
 * Copyright (c) 2011 Camiel Gubbels / Erik van der Zalm
 *
 * This program is free software: you can redistribute it and/or modify
 * it under the terms of the GNU General Public License as published by
 * the Free Software Foundation, either version 3 of the License, or
 * (at your option) any later version.
 *
 * This program is distributed in the hope that it will be useful,
 * but WITHOUT ANY WARRANTY; without even the implied warranty of
 * MERCHANTABILITY or FITNESS FOR A PARTICULAR PURPOSE.  See the
 * GNU General Public License for more details.
 *
 * You should have received a copy of the GNU General Public License
 * along with this program.  If not, see <https://www.gnu.org/licenses/>.
 *
 */
#pragma once

/**
 * Configuration.h
 *
 * Basic settings such as:
 *
 * - Type of electronics
 * - Type of temperature sensor
 * - Printer geometry
 * - Endstop configuration
 * - LCD controller
 * - Extra features
 *
 * Advanced settings can be found in Configuration_adv.h
 */
#define CONFIGURATION_H_VERSION 02000902

//===========================================================================
//============================= Getting Started =============================
//===========================================================================

/**
 * Here are some useful links to help get your machine configured and calibrated:
 *
 * Example Configs:     https://github.com/MarlinFirmware/Configurations/branches/all
 *
 * Průša Calculator:    https://blog.prusaprinters.org/calculator_3416/
 *
 * Calibration Guides:  https://reprap.org/wiki/Calibration
 *                      https://reprap.org/wiki/Triffid_Hunter%27s_Calibration_Guide
 *                      https://sites.google.com/site/repraplogphase/calibration-of-your-reprap
 *                      https://youtu.be/wAL9d7FgInk
 *
 * Calibration Objects: https://www.thingiverse.com/thing:5573
 *                      https://www.thingiverse.com/thing:1278865
 */

//===========================================================================
//============================= SCARA Printer ===============================
//===========================================================================

/**
 * X-SCARA is developed by Alex Mircescu in 2021 and is an open source
 * SCARA machine with an unique mechanical design, intented to simplify the
 * calibration process and to improve overall mechanical performance and
 * robustness for a serial SCARA machine.
 *
 * For more information:
 *    Thingiverse: https://www.thingiverse.com/thing:4500425
 *    Github: https://github.com/madl3x/x-scara
 */

#define MORGAN_SCARA
#define X_SCARA
#define X_SCARA_DEBUG       // activates debug printing (turn on by M364 D1)
#define X_SCARA_DEBUG_START_VERBOSE false

#define DEBUG_LEVELING_FEATURE

#if ENABLED(X_SCARA)
  // If movement is choppy try lowering this value
  //#define SCARA_SEGMENTS_PER_SECOND 30

  /**
   * Before raising this value, use M665 S[seg_per_sec] to decrease
   * the number of segments-per-second. Default is 200. Some deltas
   * do better with 160 or lower. It would be good to know how many
   * segments-per-second are actually possible for SCARA on AVR.
   *
   * Longer segments result in less kinematic overhead
   * but may produce jagged lines. Try 0.5mm, 1.0mm, and 2.0mm
   * and compare the difference.
   */
  #define SCARA_MIN_SEGMENT_LENGTH  0.5f
  //#define SCARA_FEEDRATE_SCALING

  // Length of inner and outer support arms. Measure arm lengths precisely.
  #define SCARA_LINKAGE_1  98.0    // (mm)
  #define SCARA_LINKAGE_2  98.0    // (mm)

  // SCARA tower offset (position of Tower relative to bed zero position)
  //#define SCARA_OFFSET_X     0      // (mm)
  //#define SCARA_OFFSET_Y    -110    // (mm)

  // Relative probe offset in angles, required for bed leveling (G29)
  #define SCARA_PROBE_OFFSET_DEGREES 20

  // For X-SCARA these are actually degrees not mmm
  // It is useful for homing, to know when the movement exceeds
  // maximum axis length.
  #define X_MAX_LENGTH (X_MAX_POS - (X_MIN_POS))
  #define Y_MAX_LENGTH (Y_MAX_POS - (Y_MIN_POS))

#endif

/**
 * MORGAN_SCARA was developed by QHARLEY in South Africa in 2012-2013.
 * Implemented and slightly reworked by JCERNY in June, 2014.
 */
//#define MORGAN_SCARA
/**
 * Mostly Printed SCARA is an open source design by Tyler Williams. See:
 *   https://www.thingiverse.com/thing:2487048
 *   https://www.thingiverse.com/thing:1241491
 */
#if EITHER(MORGAN_SCARA, MP_SCARA)
  // If movement is choppy try lowering this value
  #define SCARA_SEGMENTS_PER_SECOND 200

  // Length of inner and outer support arms. Measure arm lengths precisely.
  #define SCARA_LINKAGE_1  98.0    // (mm)
  #define SCARA_LINKAGE_2  98.0    // (mm)

  // SCARA tower offset (position of Tower relative to bed zero position)
  // This needs to be reasonably accurate as it defines the printbed position in the SCARA space.
  #define SCARA_OFFSET_X    0       // (mm)
  #define SCARA_OFFSET_Y    -110       // (mm)

  #if ENABLED(MORGAN_SCARA)

    //#define DEBUG_SCARA_KINEMATICS
    #define SCARA_FEEDRATE_SCALING  // Convert XY feedrate from mm/s to degrees/s on the fly

    // Radius around the center where the arm cannot reach
    #define MIDDLE_DEAD_ZONE_R   0  // (mm)

    #define THETA_HOMING_OFFSET  0  // Calculated from Calibration Guide and M360 / M114. See http://reprap.harleystudio.co.za/?page_id=1073
    #define PSI_HOMING_OFFSET    0  // Calculated from Calibration Guide and M364 / M114. See http://reprap.harleystudio.co.za/?page_id=1073

  #elif ENABLED(MP_SCARA)

    #define SCARA_OFFSET_THETA1  12 // degrees
    #define SCARA_OFFSET_THETA2 131 // degrees

  #endif

#endif

//===========================================================================
//==================== END ==== SCARA Printer ==== END ======================
//===========================================================================
// @section info

// Author info of this build printed to the host during boot and M115
#define STRING_CONFIG_H_AUTHOR "(none, default config)" // Who made the changes.
//#define CUSTOM_VERSION_FILE Version.h // Path from the root directory (no quotes)

/**
 * *** VENDORS PLEASE READ ***
 *
 * Marlin allows you to add a custom boot image for Graphical LCDs.
 * With this option Marlin will first show your custom screen followed
 * by the standard Marlin logo with version number and web URL.
 *
 * We encourage you to take advantage of this new feature and we also
 * respectfully request that you retain the unmodified Marlin boot screen.
 */

// Show the Marlin bootscreen on startup. ** ENABLE FOR PRODUCTION **
#define SHOW_BOOTSCREEN

// Show the bitmap in Marlin/_Bootscreen.h on startup.
//#define SHOW_CUSTOM_BOOTSCREEN

// Show the bitmap in Marlin/_Statusscreen.h on the status screen.
//#define CUSTOM_STATUS_SCREEN_IMAGE

// @section machine

/**
 * Select the serial port on the board to use for communication with the host.
 * This allows the connection of wireless adapters (for instance) to non-default port pins.
 * Serial port -1 is the USB emulated serial port, if available.
 * Note: The first serial port (-1 or 0) will always be used by the Arduino bootloader.
 *
 * :[-1, 0, 1, 2, 3, 4, 5, 6, 7]
 */
#define SERIAL_PORT -1

/**
 * Serial Port Baud Rate
 * This is the default communication speed for all serial ports.
 * Set the baud rate defaults for additional serial ports below.
 *
 * 250000 works in most cases, but you might try a lower speed if
 * you commonly experience drop-outs during host printing.
 * You may try up to 1000000 to speed up SD file transfer.
 *
 * :[2400, 9600, 19200, 38400, 57600, 115200, 250000, 500000, 1000000]
 */
#define BAUDRATE 250000
//#define BAUD_RATE_GCODE     // Enable G-code M575 to set the baud rate

/**
 * Select a secondary serial port on the board to use for communication with the host.
 * Currently Ethernet (-2) is only supported on Teensy 4.1 boards.
 * :[-2, -1, 0, 1, 2, 3, 4, 5, 6, 7]
 */
//#define SERIAL_PORT_2 -1
//#define BAUDRATE_2 250000   // Enable to override BAUDRATE

/**
 * Select a third serial port on the board to use for communication with the host.
 * Currently only supported for AVR, DUE, LPC1768/9 and STM32/STM32F1
 * :[-1, 0, 1, 2, 3, 4, 5, 6, 7]
 */
//#define SERIAL_PORT_3 1
//#define BAUDRATE_3 250000   // Enable to override BAUDRATE

// Enable the Bluetooth serial interface on AT90USB devices
//#define BLUETOOTH

// Choose the name from boards.h that matches your setup
#ifndef MOTHERBOARD
  #define MOTHERBOARD BOARD_BTT_SKR_V2_0_REV_B
#endif

// Name displayed in the LCD "Ready" message and Info menu
//#define CUSTOM_MACHINE_NAME "3D Printer"

// Printer's unique ID, used by some programs to differentiate between machines.
// Choose your own or use a service like https://www.uuidgenerator.net/version4
//#define MACHINE_UUID "00000000-0000-0000-0000-000000000000"

/**
 * Define the number of coordinated linear axes.
 * See https://github.com/DerAndere1/Marlin/wiki
 * Each linear axis gets its own stepper control and endstop:
 *
 *   Steppers: *_STEP_PIN, *_ENABLE_PIN, *_DIR_PIN, *_ENABLE_ON
 *   Endstops: *_STOP_PIN, USE_*MIN_PLUG, USE_*MAX_PLUG
 *       Axes: *_MIN_POS, *_MAX_POS, INVERT_*_DIR
 *    Planner: DEFAULT_AXIS_STEPS_PER_UNIT, DEFAULT_MAX_FEEDRATE
 *             DEFAULT_MAX_ACCELERATION, AXIS_RELATIVE_MODES,
 *             MICROSTEP_MODES, MANUAL_FEEDRATE
 *
 * :[3, 4, 5, 6]
 */
//#define LINEAR_AXES 3

/**
 * Axis codes for additional axes:
 * This defines the axis code that is used in G-code commands to
 * reference a specific axis.
 * 'A' for rotational axis parallel to X
 * 'B' for rotational axis parallel to Y
 * 'C' for rotational axis parallel to Z
 * 'U' for secondary linear axis parallel to X
 * 'V' for secondary linear axis parallel to Y
 * 'W' for secondary linear axis parallel to Z
 * Regardless of the settings, firmware-internal axis IDs are
 * I (AXIS4), J (AXIS5), K (AXIS6).
 */
#if LINEAR_AXES >= 4
  #define AXIS4_NAME 'A' // :['A', 'B', 'C', 'U', 'V', 'W']
#endif
#if LINEAR_AXES >= 5
  #define AXIS5_NAME 'B' // :['A', 'B', 'C', 'U', 'V', 'W']
#endif
#if LINEAR_AXES >= 6
  #define AXIS6_NAME 'C' // :['A', 'B', 'C', 'U', 'V', 'W']
#endif

// @section extruder

// This defines the number of extruders
// :[0, 1, 2, 3, 4, 5, 6, 7, 8]
#define EXTRUDERS 1

// Generally expected filament diameter (1.75, 2.85, 3.0, ...). Used for Volumetric, Filament Width Sensor, etc.
#define DEFAULT_NOMINAL_FILAMENT_DIA 1.75

// For Cyclops or any "multi-extruder" that shares a single nozzle.
//#define SINGLENOZZLE

// Save and restore temperature and fan speed on tool-change.
// Set standby for the unselected tool with M104/106/109 T...
#if ENABLED(SINGLENOZZLE)
  //#define SINGLENOZZLE_STANDBY_TEMP
  //#define SINGLENOZZLE_STANDBY_FAN
#endif
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

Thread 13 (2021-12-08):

Top Endstop location wrong?

iamthebest22, 2021-12-08:
Hi Alex, wondering about the endstop location at the top of the elbow assembly. Looking at the CAD of the whole arm assembly, https://myhub.autodesk360.com/ue2a87a43/g/shares/SH919a0QTf3c32634dcf530f7dd13178bc27

They are both connected to same "rods" the one that moves the hotend. Is that correct? Should the top one be at the bottom instead? (You can see the 8mm steel rods, I've attached pictures to make it clearer as I suck at explaining things)
https://www.dropbox.com/s/c88cly4qcrnnkyl/2021-12-07 16.10.55.jpg?dl=0
https://www.dropbox.com/s/0eipmqwkznc4g37/2021-12-07 16.11.00.jpg?dl=0
https://www.dropbox.com/s/yo8shwanv4avas6/2021-12-07 16.11.10.jpg?dl=0
https://www.dropbox.com/s/7gzxbvur95vhifk/2021-12-07 16.11.25.jpg?dl=0
https://www.dropbox.com/s/k9c9zb6bw78sz6t/2021-12-07 16.11.25_LI.jpg?dl=0 (This one shows if the endstop should be moved to the one rod below).
I've build the whole thing, and this is the only thing that confuse me, because right now when I move the hotend arm, both endstops move, which I don't think should be the case? Thanks.

iamthebest22, 2021-12-09:
Nvm, I've asked other scara, can be either options,.

madl3x, 2021-12-16:
I know you closed this, but I will answer anyway, for posterity.
The shoulder (distal arm) driving axis should not move when you move the elbow (proximal arm).

That driving axis should be on top of the arm, where the shoulder starts. There is another axis colinear with this one, on the bottom of the arm, that is indeed driving the elbow, and is providing another 1/3 reduction. That is the one that you noticed moving when you move the tip.

You should put the shoulder endstop where the shoulder driving axis is, the one that moves independently over the elbow.
Hope it helps.

iamthebest22, 2021-12-16:
thankyou, that really clears it up. I've flipped the orientation, than the CAD files showed, so yes, the top endstop is now on the shoulder endstop, and doesn't move when I move the hotend arm. the lower endstop is now on the one that moves the hotend arms. Thanks! Now to sort it out for RRF.

Closed 2021-12-09.

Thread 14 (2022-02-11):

I wonder about direction of shoulder and elbow when press +X , -X and +Y, -Y on pronterface test

ToonKru3, 2022-02-11:
**Right Now I have use your X-scara firmware.I know how to set INVERT my motor but I confuse what is the correct direction.I test on Pronterface and Repetier-Host.My Question is**
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

1. When i press +X  or -X what direction could be ?
2. and +Y and -Y direction

ToonKru3, 2022-02-17:
and how to set up "start gcode" from repetier or other slicer program to start printer

madl3x, 2022-02-20:
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

madl3x, 2022-02-20:
`and how to set up "start gcode" from repetier or other slicer program to start printer

You could use the defaults for a regular cartesian printer. The only special code I use for a startup is lifting the nozzle up 15 mm before homing. That is because I have a heated bed that the arm could crash into when G28 is run.

Startup g-code:
```
;Home all axis
G28
;Move the arm away from print area
M361 S-90 E90
;Move the arm up 15mm
G1 Z15.0 F6000
;Prime the extruder
G92 E0
G1 F200 E5
G92 E0
;Start printing..
```
End g-code:
```;Move the arm away from print area
G0 F3000 ; set feedrate
M361 S-90 E90
;Stop heaters
M104 S0
M140 S0
;Retract the filament
G92 E3
G1 E-3 F300
; Lower it
G0 Z-6
; Disable steppers (arm will drop)
M84
```

ToonKru3, 2022-02-20:
this is for 0.4 beta firmware?  And i have another problem with wrong geometry curve trapezoid
![Uploading 16453747932188852240887495335396.jpg…]()

ToonKru3, 2022-02-20:
And 0.4 firmwarm i have to calibrate m362 e0 s0 or not important on 0.4 just homing with endstop and print right?

ToonKru3, 2022-02-21:
Right now i stright my scara arm and then calibrate with gcode m362 e0 s0 and use g0 x0 y0 nest hotend is center of my robot but when I test with repetier host  X+ and X- button.they don't move stright line but curve line and when i test print squre it's curve again

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

It's depending on "number teeth" of shoulder gear and elbow gear ? Like need to have even or odd number of teeth ?
 my scara I design with Shoulder 223 teeth and Elbow 144 teeth or not this case but something in firmware ?

ToonKru3, 2022-02-21:
This is my edit firmware

/**
 * Marlin 3D Printer Firmware
 * Copyright (c) 2020 MarlinFirmware [https://github.com/MarlinFirmware/Marlin]
 *
 * Based on Sprinter and grbl.
 * Copyright (c) 2011 Camiel Gubbels / Erik van der Zalm
 *
 * This program is free software: you can redistribute it and/or modify
 * it under the terms of the GNU General Public License as published by
 * the Free Software Foundation, either version 3 of the License, or
 * (at your option) any later version.
 *
 * This program is distributed in the hope that it will be useful,
 * but WITHOUT ANY WARRANTY; without even the implied warranty of
 * MERCHANTABILITY or FITNESS FOR A PARTICULAR PURPOSE.  See the
 * GNU General Public License for more details.
 *
 * You should have received a copy of the GNU General Public License
 * along with this program.  If not, see <http://www.gnu.org/licenses/>.
 *
 */
#pragma once

/**
 * Configuration.h
 *
 * Basic settings such as:
 *
 * - Type of electronics
 * - Type of temperature sensor
 * - Printer geometry
 * - Endstop configuration
 * - LCD controller
 * - Extra features
 *
 * Advanced settings can be found in Configuration_adv.h
 *
 */
#define CONFIGURATION_H_VERSION 020005

//===========================================================================
//============================= Getting Started =============================
//===========================================================================

/**
 * Here are some standard links for getting your machine calibrated:
 *
 * http://reprap.org/wiki/Calibration
 * http://youtu.be/wAL9d7FgInk
 * http://calculator.josefprusa.cz
 * http://reprap.org/wiki/Triffid_Hunter%27s_Calibration_Guide
 * http://www.thingiverse.com/thing:5573
 * https://sites.google.com/site/repraplogphase/calibration-of-your-reprap
 * http://www.thingiverse.com/thing:298812
 */

//===========================================================================
//============================= SCARA Printer ===============================
//===========================================================================

/**
 * X-SCARA is developed by Alex Mircescu in 2021 and is an open source
 * SCARA machine with an unique mechanical design, intented to simplify the
 * calibration process and to improve overall mechanical performance and
 * robustness for a serial SCARA machine.
 *
 * For more information:
 *    Thingiverse: https://www.thingiverse.com/thing:4500425
 *    Github: https://github.com/madl3x/x-scara
 */

#define SCARA
#define X_SCARA
#define X_SCARA_DEBUG       // activates debug printing (turn on by M364 D1)
#define X_SCARA_DEBUG_START_VERBOSE false

#define DEBUG_LEVELING_FEATURE

#if ENABLED(X_SCARA)
  // If movement is choppy try lowering this value
  #define SCARA_SEGMENTS_PER_SECOND 30

  /**
   * Before raising this value, use M665 S[seg_per_sec] to decrease
   * the number of segments-per-second. Default is 200. Some deltas
   * do better with 160 or lower. It would be good to know how many
   * segments-per-second are actually possible for SCARA on AVR.
   *
   * Longer segments result in less kinematic overhead
   * but may produce jagged lines. Try 0.5mm, 1.0mm, and 2.0mm
   * and compare the difference.
   */
  #define SCARA_MIN_SEGMENT_LENGTH  0.5f
  //#define SCARA_FEEDRATE_SCALING

  // Length of inner and outer support arms. Measure arm lengths precisely.
  #define SCARA_LINKAGE_1  175     // (mm)
  #define SCARA_LINKAGE_2  153     // (mm)

  // SCARA tower offset (position of Tower relative to bed zero position)
  #define SCARA_OFFSET_X   0     // (mm)
  #define SCARA_OFFSET_Y   -120    // (mm)

  // Relative probe offset in angles, required for bed leveling (G29)
  #define SCARA_PROBE_OFFSET_DEGREES 20

  // For X-SCARA these are actually degrees not mmm
  // It is useful for homing, to know when the movement exceeds
  // maximum axis length.
  #define X_MAX_LENGTH 300
  #define Y_MAX_LENGTH 300

#endif

/**
 * MORGAN_SCARA was developed by QHARLEY in South Africa in 2012-2013.
 * Implemented and slightly reworked by JCERNY in June, 2014.
 */
//#define MORGAN_SCARA
/**
 * Mostly Printed SCARA is an open source design by Tyler Williams. See:
 *   https://www.thingiverse.com/thing:2487048
 *   https://www.thingiverse.com/thing:1241491
 */
#if EITHER(MORGAN_SCARA, MP_SCARA)
  // If movement is choppy try lowering this value
  #define SCARA_SEGMENTS_PER_SECOND 200

  // Length of inner and outer support arms. Measure arm lengths precisely.
  #define SCARA_LINKAGE_1  98.0    // (mm)
  #define SCARA_LINKAGE_2  98.0    // (mm)

  // SCARA tower offset (position of Tower relative to bed zero position)
  // This needs to be reasonably accurate as it defines the printbed position in the SCARA space.
  #define SCARA_OFFSET_X    0       // (mm)
  #define SCARA_OFFSET_Y    0       // (mm)

  #if ENABLED(MORGAN_SCARA)

    //#define DEBUG_SCARA_KINEMATICS
    #define SCARA_FEEDRATE_SCALING  // Convert XY feedrate from mm/s to degrees/s on the fly

    // Radius around the center where the arm cannot reach
    #define MIDDLE_DEAD_ZONE_R   0  // (mm)

    #define THETA_HOMING_OFFSET  0  // Calculated from Calibration Guide and M360 / M114. See http://reprap.harleystudio.co.za/?page_id=1073
    #define PSI_HOMING_OFFSET    0  // Calculated from Calibration Guide and M364 / M114. See http://reprap.harleystudio.co.za/?page_id=1073

  #elif ENABLED(MP_SCARA)

    #define SCARA_OFFSET_THETA1  12 // degrees
    #define SCARA_OFFSET_THETA2 131 // degrees

  #endif

#endif

//===========================================================================
//==================== END ==== SCARA Printer ==== END ======================
//===========================================================================

// @section info

// Author info of this build printed to the host during boot and M115
#define STRING_CONFIG_H_AUTHOR "Supadett Pinsuwannabut" // Who made the changes.

#define CUSTOM_VERSION_FILE Version.h // Path from the root directory (no quotes)

/**
 * *** VENDORS PLEASE READ ***
 *
 * Marlin allows you to add a custom boot image for Graphical LCDs.
 * With this option Marlin will first show your custom screen followed
 * by the standard Marlin logo with version number and web URL.
 *
 * We encourage you to take advantage of this new feature and we also
 * respectfully request that you retain the unmodified Marlin boot screen.
 */

// Show the Marlin bootscreen on startup. ** ENABLE FOR PRODUCTION **
#define SHOW_BOOTSCREEN

// Show the bitmap in Marlin/_Bootscreen.h on startup.
//#define SHOW_CUSTOM_BOOTSCREEN

// Show the bitmap in Marlin/_Statusscreen.h on the status screen.
//#define CUSTOM_STATUS_SCREEN_IMAGE

// @section machine

/**
 * Select the serial port on the board to use for communication with the host.
 * This allows the connection of wireless adapters (for instance) to non-default port pins.
 * Serial port -1 is the USB emulated serial port, if available.
 * Note: The first serial port (-1 or 0) will always be used by the Arduino bootloader.
 *
 * :[-1, 0, 1, 2, 3, 4, 5, 6, 7]
 */
#define SERIAL_PORT 0

/**
 * Select a secondary serial port on the board to use for communication with the host.
 * :[-1, 0, 1, 2, 3, 4, 5, 6, 7]
 */
//#define SERIAL_PORT_2 -1

/**
 * This setting determines the communication speed of the printer.
 *
 * 250000 works in most cases, but you might try a lower speed if
 * you commonly experience drop-outs during host printing.
 * You may try up to 1000000 to speed up SD file transfer.
 *
 * :[2400, 9600, 19200, 38400, 57600, 115200, 250000, 500000, 1000000]
 */
#define BAUDRATE 115200

// Enable the Bluetooth serial interface on AT90USB devices
//#define BLUETOOTH

// Choose the name from boards.h that matches your setup
#ifndef MOTHERBOARD
  #define MOTHERBOARD BOARD_MKS_GEN_L
#endif

// Name displayed in the LCD "Ready" message and Info menu
#define CUSTOM_MACHINE_NAME "Scara 3D"

// Printer's unique ID, used by some programs to differentiate between machines.
// Choose your own or use a service like http://www.uuidgenerator.net/version4
//#define MACHINE_UUID "00000000-0000-0000-0000-000000000000"

// @section extruder

// This defines the number of extruders
// :[1, 2, 3, 4, 5, 6, 7, 8]
#define EXTRUDERS 1

// Generally expected filament diameter (1.75, 2.85, 3.0, ...). Used for Volumetric, Filament Width Sensor, etc.
#define DEFAULT_NOMINAL_FILAMENT_DIA 1.75

// For Cyclops or any "multi-extruder" that shares a single nozzle.
//#define SINGLENOZZLE

/**
 * Průša MK2 Single Nozzle Multi-Material Multiplexer, and variants.
 *
 * This device allows one stepper driver on a control board to drive
 * two to eight stepper motors, one at a time, in a manner suitable
 * for extruders.
 *
 * This option only allows the multiplexer to switch on tool-change.
 * Additional options to configure custom E moves are pending.
 */
//#define MK2_MULTIPLEXER
#if ENABLED(MK2_MULTIPLEXER)
  // Override the default DIO selector pins here, if needed.
  // Some pins files may provide defaults for these pins.
  //#define E_MUX0_PIN 40  // Always Required
  //#define E_MUX1_PIN 42  // Needed for 3 to 8 inputs
  //#define E_MUX2_PIN 44  // Needed for 5 to 8 inputs
#endif

/**
 * Prusa Multi-Material Unit v2
 *
 * Requires NOZZLE_PARK_FEATURE to park print head in case MMU unit fails.
 * Requires EXTRUDERS = 5
 *
 * For additional configuration see Configuration_adv.h
 */
//#define PRUSA_MMU2

// A dual extruder that uses a single stepper motor
//#define SWITCHING_EXTRUDER
#if ENABLED(SWITCHING_EXTRUDER)
  #define SWITCHING_EXTRUDER_SERVO_NR 0
  #define SWITCHING_EXTRUDER_SERVO_ANGLES { 0, 90 } // Angles for E0, E1[, E2, E3]
  #if EXTRUDERS > 3
    #define SWITCHING_EXTRUDER_E23_SERVO_NR 1
  #endif
#endif
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

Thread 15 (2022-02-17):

When i invert X & Y motor to correct direction.endstop homing is wrong direction.

ToonKru3, 2022-02-17:
follow the topics above how to flip the direction of endstop homing.I use X-scara 4.0 firmware

Closed 2022-02-21.

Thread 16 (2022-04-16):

Marlin 2.0.9.3

Riverolf, 2022-04-16:
I had to download the newest marlin 2.0.9.3 to get my skr e3 v3 board to come up in the beard definitions.
When using this version, i follow the config readme file, and the line #define SCARA throws an error, saying that it is nor MORGAN_SCARA, So I change it to this. Is this correct?

I also cannot use the #define X_MAX_LENGTH 300 and #define Y_MAX_LENGTH 300 line. It throws an error.

Everytring else is able to compile,but I have not been able to test the machine yet. I am missing some parts.
Will this be okay to use, or do I need to change something more?

Riverolf, 2022-05-02:
I managed to get the printer up and running using MP_SCARA in marlin. But I cannot find how to define elbow crosstalk. I see that this has been taken care of in the X-SCARA code. Does anybody know how to do this in MP_SCARA?

gnmrc-s, 2022-05-03:
You have to add the crosstalk in the kinematics file, like it has been done in the x scara, follow the calculation that madl3x has done.
I also tried with MP_SCARA configuration, by how to mechatronics but I wasn't as lucky as you, my arm is not stopped by the endstops during homing, even if they work properly.

Riverolf, 2022-05-03:
I am one step further with the MP_SCARA side of things.
I changed the scara.cpp file in line 129:

// Angle of Arm2
    PSI = ATAN2(S2, C2);
    PSI = PSI + THETA/3; //RSTROMO

I added the line where RSTROMO is commented. This seems to make the prints look more like they should.
i will be testing it the next few days.

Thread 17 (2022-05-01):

Klipper firmware

Riverolf, 2022-05-01:
Has anybody made an effort to make klipper firmware for this printer?
[https://l.facebook.com/l.php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]-R&c[0]=AT2O4dEJ5zFfspLS1dx8d6K6DJ8ODtcojti8uXWrlCcBQY504P4EgU0Liv2O5C7gRrQp2cFWBYfonO4PN8jBpFg7pfV8tpRfU5ao-9N3sl3P02gUkaaPpFxFH2K9zE0Gr10q20vSj_QXn7nvXw6OvxUhkYvceKAcgON2v_2avVYZRpuBHmw5QRu0cgKSy8NonshQYp7HaQ3qBNrbycI](adding new kinematics)

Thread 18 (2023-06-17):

same issue as vojjta

Stewie-040882, 2023-06-17:
whats the point of listing how to construct it, and not list the board ect? i would give this a try, but without a way to control it i'll of wasted hours and money on a brick.

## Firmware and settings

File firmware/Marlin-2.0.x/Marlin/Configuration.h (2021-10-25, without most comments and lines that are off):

#pragma once
#define CONFIGURATION_H_VERSION 020005
#define SCARA
#define X_SCARA
#define X_SCARA_DEBUG       // activates debug printing (turn on by M364 D1)
#define X_SCARA_DEBUG_START_VERBOSE false
#define DEBUG_LEVELING_FEATURE
  #define SCARA_SEGMENTS_PER_SECOND 30
  #define SCARA_MIN_SEGMENT_LENGTH  0.5f
  #define SCARA_LINKAGE_1  98.0    // (mm)
  #define SCARA_LINKAGE_2  98.0    // (mm)
  #define SCARA_OFFSET_X     0      // (mm)
  #define SCARA_OFFSET_Y    -110    // (mm)
  #define SCARA_PROBE_OFFSET_DEGREES 20
  #define X_MAX_LENGTH 300
  #define Y_MAX_LENGTH 300
#if EITHER(MORGAN_SCARA, MP_SCARA)
  #define SCARA_SEGMENTS_PER_SECOND 200
  #define SCARA_LINKAGE_1  98.0    // (mm)
  #define SCARA_LINKAGE_2  98.0    // (mm)
  #define SCARA_OFFSET_X    0       // (mm)
  #define SCARA_OFFSET_Y    0       // (mm)
  #if ENABLED(MP_SCARA)
    #define SCARA_OFFSET_THETA1  12 // degrees
    #define SCARA_OFFSET_THETA2 131 // degrees
  #endif
#endif
#define STRING_CONFIG_H_AUTHOR "(Alex Mircescu, Ian-2021)" // Who made the changes.
#define CUSTOM_VERSION_FILE Version.h // Path from the root directory (no quotes)
#define SHOW_BOOTSCREEN
#define SERIAL_PORT 0
#define BAUDRATE 250000
  #define MOTHERBOARD BOARD_SANGUINOLOLU_12
#define CUSTOM_MACHINE_NAME "X-SCARA"
#define EXTRUDERS 1
#define DEFAULT_NOMINAL_FILAMENT_DIA 3.0
#define TEMP_SENSOR_0 1
#define TEMP_SENSOR_1 0
#define TEMP_SENSOR_2 0
#define TEMP_SENSOR_3 0
#define TEMP_SENSOR_4 0
#define TEMP_SENSOR_5 0
#define TEMP_SENSOR_6 0
#define TEMP_SENSOR_7 0
#define TEMP_SENSOR_BED 1
#define TEMP_SENSOR_PROBE 0
#define TEMP_SENSOR_CHAMBER 0
#define DUMMY_THERMISTOR_998_VALUE 25
#define DUMMY_THERMISTOR_999_VALUE 100
#define MAX_REDUNDANT_TEMP_SENSOR_DIFF 10
#define TEMP_RESIDENCY_TIME 3  // (seconds) Time to wait for hotend to "settle" in M109
#define TEMP_HYSTERESIS 2       // (°C) Temperature proximity considered "close enough" to the target
#define TEMP_WINDOW     1       // (°C) Temperature proximity for the "temperature reached" timer
#define TEMP_BED_RESIDENCY_TIME  0  // (seconds) Time to wait for bed to "settle" in M190
#define TEMP_BED_WINDOW          1  // (°C) Temperature proximity for the "temperature reached" timer
#define TEMP_BED_HYSTERESIS      3  // (°C) Temperature proximity considered "close enough" to the target
#define HEATER_0_MINTEMP   5
#define HEATER_1_MINTEMP   5
#define HEATER_2_MINTEMP   5
#define HEATER_3_MINTEMP   5
#define HEATER_4_MINTEMP   5
#define HEATER_5_MINTEMP   5
#define HEATER_6_MINTEMP   5
#define HEATER_7_MINTEMP   5
#define BED_MINTEMP        5
#define HEATER_0_MAXTEMP 275
#define HEATER_1_MAXTEMP 275
#define HEATER_2_MAXTEMP 275
#define HEATER_3_MAXTEMP 275
#define HEATER_4_MAXTEMP 275
#define HEATER_5_MAXTEMP 275
#define HEATER_6_MAXTEMP 275
#define HEATER_7_MAXTEMP 275
#define BED_MAXTEMP      110
#define PIDTEMP
#define BANG_MAX 255     // Limits current to nozzle while in bang-bang mode; 255=full current
#define PID_MAX BANG_MAX // Limits current to nozzle while PID is active (see PID_FUNCTIONAL_RANGE below); 255=full current
#define PID_K1 0.95      // Smoothing factor within any PID loop
  #define PID_FUNCTIONAL_RANGE 20 // If the temperature difference between the target temperature and the actual temperature
  #define DEFAULT_Kp 24.5
  #define DEFAULT_Ki 1.72
  #define DEFAULT_Kd 87.73
#define PIDTEMPBED
#define MAX_BED_POWER 255 // limits duty cycle to bed; 255=full current
  #define DEFAULT_bedKp 630.14
  #define DEFAULT_bedKi 121.71
  #define DEFAULT_bedKd 815.64
#define PREVENT_LENGTHY_EXTRUDE
#define EXTRUDE_MAXLENGTH 200
#define THERMAL_PROTECTION_HOTENDS // Enable thermal protection for all extruders
#define THERMAL_PROTECTION_BED     // Enable thermal protection for the heated bed
#define THERMAL_PROTECTION_CHAMBER // Enable thermal protection for the heated chamber
#define USE_XMIN_PLUG
#define USE_YMIN_PLUG
#define USE_ZMIN_PLUG
#define X_MIN_ENDSTOP_INVERTING true // Set to true to invert the logic of the endstop.
#define Y_MIN_ENDSTOP_INVERTING true // Set to true to invert the logic of the endstop.
#define Z_MIN_ENDSTOP_INVERTING true // Set to true to invert the logic of the endstop.
#define X_MAX_ENDSTOP_INVERTING false // Set to true to invert the logic of the endstop.
#define Y_MAX_ENDSTOP_INVERTING false // Set to true to invert the logic of the endstop.
#define Z_MAX_ENDSTOP_INVERTING false // Set to true to invert the logic of the endstop.
#define Z_MIN_PROBE_ENDSTOP_INVERTING true // Set to true to invert the logic of the probe.
#define X_DRIVER_TYPE  LV8729
#define Y_DRIVER_TYPE  LV8729
#define Z_DRIVER_TYPE  A4988
#define DEFAULT_AXIS_STEPS_PER_UNIT   { 26.666666666666667, 80, 400, 418.5 }
#define X_SCARA_ELBOW_CROSSTALK_RATIO 3  // 60 % 20 = 3}
#define DEFAULT_MAX_FEEDRATE          { 300, 300, 15, 30 }
#define DEFAULT_MAX_ACCELERATION      { 1000, 1000, 100, 20000 }
#define DEFAULT_ACCELERATION          1000    // X, Y, Z and E acceleration for printing moves
#define DEFAULT_RETRACT_ACCELERATION  1000    // E acceleration for retracts
#define DEFAULT_TRAVEL_ACCELERATION   1000    // X, Y, Z acceleration for travel (non printing) moves
#define CLASSIC_JERK
  #define DEFAULT_XJERK  5.0
  #define DEFAULT_YJERK  5.0
  #define DEFAULT_ZJERK  0.3
#define DEFAULT_EJERK    3.0  // May be used by Linear Advance
#define Z_MIN_PROBE_USES_Z_MIN_ENDSTOP_PIN
#define NOZZLE_AS_PROBE
#define NOZZLE_TO_PROBE_OFFSET { 0, 0, 0 }
#define MIN_PROBE_EDGE 15
#define XY_PROBE_SPEED HOMING_FEEDRATE_XY
#define Z_PROBE_SPEED_FAST HOMING_FEEDRATE_Z
#define Z_PROBE_SPEED_SLOW (Z_PROBE_SPEED_FAST / 2)
#define Z_CLEARANCE_DEPLOY_PROBE    5 // Z Clearance for Deploy/Stow
#define Z_CLEARANCE_BETWEEN_PROBES  5 // Z Clearance between probe points
#define Z_CLEARANCE_MULTI_PROBE     5 // Z Clearance between multiple probes
#define Z_PROBE_LOW_POINT          -2 // Farthest distance below the trigger-point to go before stopping
#define Z_PROBE_OFFSET_RANGE_MIN -20
#define Z_PROBE_OFFSET_RANGE_MAX 20
#define X_ENABLE_ON 0
#define Y_ENABLE_ON 0
#define Z_ENABLE_ON 0
#define E_ENABLE_ON 0 // For all extruders
#define DISABLE_X false
#define DISABLE_Y false
#define DISABLE_Z false
#define DISABLE_E false             // For all extruders
#define DISABLE_INACTIVE_EXTRUDER   // Keep only the active extruder enabled
#define INVERT_X_DIR false
#define INVERT_Y_DIR true
#define INVERT_Z_DIR false
#define INVERT_E0_DIR false
#define INVERT_E1_DIR false
#define INVERT_E2_DIR false
#define INVERT_E3_DIR false
#define INVERT_E4_DIR false
#define INVERT_E5_DIR false
#define INVERT_E6_DIR false
#define INVERT_E7_DIR false
#define Z_HOMING_HEIGHT  4      // (mm) Minimal Z height before homing (G28) for Z clearance above the bed, clamps, ...
#define X_HOME_DIR -1
#define Y_HOME_DIR -1
#define Z_HOME_DIR -1
#define X_BED_SIZE 90
#define Y_BED_SIZE 90
#define X_MIN_POS (0-X_BED_SIZE/2)
#define Y_MIN_POS (0-Y_BED_SIZE/2)
#define Z_MIN_POS 0
#define X_MAX_POS (X_MIN_POS + X_BED_SIZE)
#define Y_MAX_POS (Y_MIN_POS + Y_BED_SIZE)
#define Z_MAX_POS 100
#define MIN_SOFTWARE_ENDSTOPS
  #define MIN_SOFTWARE_ENDSTOP_X
  #define MIN_SOFTWARE_ENDSTOP_Y
  #define MIN_SOFTWARE_ENDSTOP_Z
#define MAX_SOFTWARE_ENDSTOPS
  #define MAX_SOFTWARE_ENDSTOP_X
  #define MAX_SOFTWARE_ENDSTOP_Y
  #define MAX_SOFTWARE_ENDSTOP_Z
#define AUTO_BED_LEVELING_UBL
#define RESTORE_LEVELING_AFTER_G28
  #define ENABLE_LEVELING_FADE_HEIGHT
  #define SEGMENT_LEVELED_MOVES
  #define LEVELED_SEGMENT_LENGTH 5.0 // (mm) Length of all segments (except the last one)
  #define MESH_INSET 20              // Set Mesh bounds as an inset region of the bed
  #define GRID_MAX_POINTS_X 3      // Don't use more than 15 points per axis, implementation limited.
  #define GRID_MAX_POINTS_Y GRID_MAX_POINTS_X
  #define UBL_MESH_EDIT_MOVES_Z     // Sophisticated users prefer no movement of nozzle
  #define UBL_SAVE_ACTIVE_ON_M500   // Save the currently active mesh in the current slot on M500
#define BED_CENTER_AT_0_0
#define MANUAL_X_HOME_POS 0
#define MANUAL_Y_HOME_POS 0
#define HOMING_FEEDRATE_XY (60*60)
#define HOMING_FEEDRATE_Z  (4*60)
#define VALIDATE_HOMING_ENDSTOPS
#define EEPROM_SETTINGS     // Persistent storage with M500 and M501
#define EEPROM_CHITCHAT       // Give feedback on EEPROM commands. Disable to save PROGMEM.
#define HOST_KEEPALIVE_FEATURE        // Disable this if your host doesn't like keepalive messages
#define DEFAULT_KEEPALIVE_INTERVAL 2  // Number of seconds between "busy" messages. Set with M113.
#define BUSY_WHILE_HEATING            // Some hosts require "busy" messages even during heating
#define PREHEAT_1_LABEL       "PLA"
#define PREHEAT_1_TEMP_HOTEND 180
#define PREHEAT_1_TEMP_BED     70
#define PREHEAT_1_FAN_SPEED   255 // Value from 0 to 255
#define PREHEAT_2_LABEL       "ABS"
#define PREHEAT_2_TEMP_HOTEND 240
#define PREHEAT_2_TEMP_BED    100
#define PREHEAT_2_FAN_SPEED   255 // Value from 0 to 255
#define PRINTJOB_TIMER_AUTOSTART
#define LCD_LANGUAGE en
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

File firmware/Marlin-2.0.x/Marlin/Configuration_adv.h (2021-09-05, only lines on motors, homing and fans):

#define E0_AUTO_FAN_PIN -1
#define E1_AUTO_FAN_PIN -1
#define E2_AUTO_FAN_PIN -1
#define E3_AUTO_FAN_PIN -1
#define E4_AUTO_FAN_PIN -1
#define E5_AUTO_FAN_PIN -1
#define CHAMBER_AUTO_FAN_PIN -1
#define X_HOME_BUMP_MM 3
#define Y_HOME_BUMP_MM 3
#define Z_HOME_BUMP_MM 3
#define HOMING_BUMP_DIVISOR { 2, 2, 4 }  // Re-Bump Speed Divisor (Divides the Homing Feedrate)
#define MICROSTEP_MODES { 16, 16, 16, 16, 16, 16 } // [1,2,4,8,16]
#define DIGIPOT_I2C_MOTOR_CURRENTS { 1.0, 1.0, 1.0, 1.0, 1.0, 1.0, 1.0, 1.0 }  //  AZTEEG_X3_PRO

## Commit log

2020-06-25 frame and arm assembly instruction and pictures
    [Arm_Base_MotorPlate_1.0.0.stl, Arm_Base_ZHub_Bottom_1.0.0.stl, Arm_Base_ZHub_Top_1.0.0.stl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]
2020-06-26 added arm assembly previews
2020-11-28 issue #2 - fixed overlap of extruder's fan mount
    [Arm_EMount_Fan_1.0.0.stl, Arm_EMount_Fan_1.0.1.stl]
2020-11-28 issue #3 - fixed typo in frame's tip connector; added left and right versions for the frame side connector
    [Frame_Plate_SideConnector_1.0.0.stl, Frame_Plate_Side_RodClamp_Left_1.0.1.stl, Frame_Plate_Side_RodClamp_Right_1.0.1.stl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]
2021-01-12 alpha firmware release
    [Configuration.h, Configuration_adv.h]
2021-01-16 firmware version 0,2A; fixed 'scara is printing' error for M commands; X axis is inverted (previously it was printing mirrored parts;
2021-02-14 hardware revision 2
    [Arm_Base_MotorPlate_1.0.0.stl, Arm_Base_MotorPlate_1.1.2.stl, Arm_EMount_Base_ABL_1.0.0.stl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]
2021-02-14 hardware revision 3 - added endstop mount
    [Arm_Endstop_1.0.3.stl]
2021-02-14 added test part accessory
    [Test_hardware_fit_1.0.4.stl]
2021-02-14 updated landing README.md, removed unused images
2021-02-17 revision 5: added new accessory: heated bed
    [Acc_FixedBedMount_AlternativeArm_1.0.5.stl, Acc_FixedBedMount_Arm_1.0.5.stl, Acc_FixedBedMount_HeaterSupport_1.0.5.stl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]
2021-09-05 FW 0.4 Beta: ihoming, UBL leveling, EEPROM settings (origin offset, home offset, delta seg sec, delta min seg), coord.transf. modes, planner and motion adjustements
    [Configuration.h, Configuration_adv.h]
2021-09-09 firmware 0.4.1 - fixed G0 bed leveling
2021-09-09 fixed arm BOM
2021-09-09 adding bed mount to the list of accessories
2021-09-19 fixing #7 - frame BOM contains an incorrect number of profiles for the smaller 60 mm segments
2021-09-23 fixing stl count to print for arm
2021-09-23 Updated printed part table for frame
2021-10-24 added ELBOW_REDUCTION_RATIO config
    [Configuration.h]
2021-10-25 renamed config parameter, added sanity check.
    [Configuration.h]

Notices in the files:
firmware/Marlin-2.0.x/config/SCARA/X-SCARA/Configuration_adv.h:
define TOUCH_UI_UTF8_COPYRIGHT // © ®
